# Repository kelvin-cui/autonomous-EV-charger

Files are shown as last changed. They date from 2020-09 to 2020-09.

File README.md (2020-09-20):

# autonomous-EV-charger

## Background
With the climate crisis that's happening right now, it's now more important than ever to take action and start adopting sustainable practices before we cause irreversable damage to our planet. A popular trend is the shift towards electric vehicles, and in an effort to make these vehicles more attractive, our team was tasked with creating an autonomous charger robot that would automatically find, and plug the charging line into the car after the car is parked. Our team is comprised of Anton Liu, Haoran Jayce Wang, and Kelvin Cui, and this project was created for our ESC204 (Praxis 3) class from the University of Toronto Engineering Science program.

autonomous

## Objective
Our objective was to create a robot that could locate the charging port of an electric vehicle, and plug in a standard charging plug. We wanted the robot to take up as little space as possible, be consistent and reliable, all while constraining ourselves to a budget of $300 CAD. 
Main

## How it works
The robot is controlled by a raspberry pi, using computer vision to determine the location of the port. Two IR distance sensors on each side of the bot determine the yaw of the bot with respect to the side of the car, and allow the bot to align itself perpendicularly. Stepper motors arranged in a square at the bottom of the bot allow the robot to rotate, and move in a straight line until it's directly in front of the charging port. Another stepper motor attached to a lead screw control a scissor lift mechanism that lifts the charging handle to the same height as the port. Finally, the robot moves forward to plug the handle in, where a limit switch lets the bot know when the handle is fully plugged in.
Plug-Quarter-View

## Design Process
In order to design this robot, we started by defining our stakeholders, our objectives, and our metrics to measure these objectives. Using this model, we started multiple rounds of design, going through many different alternatives until we finally arrived at our solution. If you're interested, you can see the detailed request for proposal here : 

**[Request for Proposal](https://github.com/ntnox/autonomous-EV-charger/blob/master/Request%20for%20Proposal.pdf)**

### Hardware Choice
Given our time and budget constraints, most of our electronics and sensors are simple, off the shelf components. We chose a raspberry pi as it allowed us to do complex computer vision analysis to find the charging port, with a raspberry pi camera. We chose IR distance sensors over ultrasonic sensors as they were more consistent, and delivered more accurate results in our range. For motors, we chose stepper motors, despite their increased complexity (more power draw and stepper motor drivers), as it would allow for finer control when compared to simple DC motors. Finally, we decided to go with a fixed power supply rather than a battery pack simply because it better fit our budgetary constraints. Finally, the omni-wheels were chosen to allow the rover to move freely, and rotate on the spot.

### Physical Design
Next came our design. We decided to model the entirety of our design, and take advantage of the rapid prototyping tools we had in our disposal. With a model, we were able to either lazer cut or 3D print all of our components.

Mechanical-CAD

While creating the model, we needed to make sure that from a strength perspective, our design would be feasible. As a result, we did FEA anaylsis of all of our structural parts to ensure that the parts wouldn't fail.

CAD FEA

### Electronic Design
For electrical design, we wanted to make sure that it was relaible, and we wanted it to be as easily repairable as possible should anything go wrong. As a result, our circuitry design is based on solderable breadboards for secure connections, with color coded wiring to easily distinguish the ciruits. In particular, since we had two power rails (5V and 24V), we used red wiring for all 5V, white for all 24V, and black for all ground. The main circuit was connected to the sensors, motors, and raspberry pi via JST headers, and could be easily taken out of the robot for repairs.

Electrical-Circuitry

### Software Design
- All the software is written in Python and executed by the onboard Raspberry Pi Zero. The goal of the software was to be able to autonomously detect the charging port and be able to align and navigate the charger into the charging port. The last developments made in the area of port detection used OpenCV to process frames from a live video feed to identify set markers on the charging port prototype. 
- Various methods were prototyped to experiment with the best approach to reliably identify and localize the robot with respect to the port through OpenCV that can be read about in the Programming folder, but the finalized approach was to use a red rectangle marked ontop of the port as the localization identifier. This method is the most reliable as our approach was to create a mask that only allowed pixels that match the redness of the marker and ultimately identify the contour of the rectangle in that mask. Since we knew exactly where our camera was placed on the robot, with some calibration and testing, we can then use the location of the rectuangular contour on the frame to localize the robot. To maximize the frames per second the robot is able to process using OpenCV, the task of generating the video stream from the camera and the processing of frames were completed on multiple threads or paralleled computations. This method was able to significantly improve our processed video stream from less than 10 fps to more than 15 fps.

- To control the movement of the robot, we utilized the integrated GPIO library in Python to output corresponding digital signals to control stepper motors as required
- Wireless communication for remote control of the robot from a laptop when required was built using the socket library in Python to create a server for sending desired commands to the rasberry pi and placing both the control laptop and the raspberry pi to be on one hotspot network so that they could communicate over the shared wifi. 

### Project Management
- Trello was used to manage this project, and this includes aspects such as due dates, person assigned, descriptions, categorization, etc. It gives us a clear view of the status of the project, and keeps us on track to complete it. We have also included a "Risks" section to identify potential failure modes of the design, and planned solutions for them. With trello, we were able to keep the project organized and efficient.

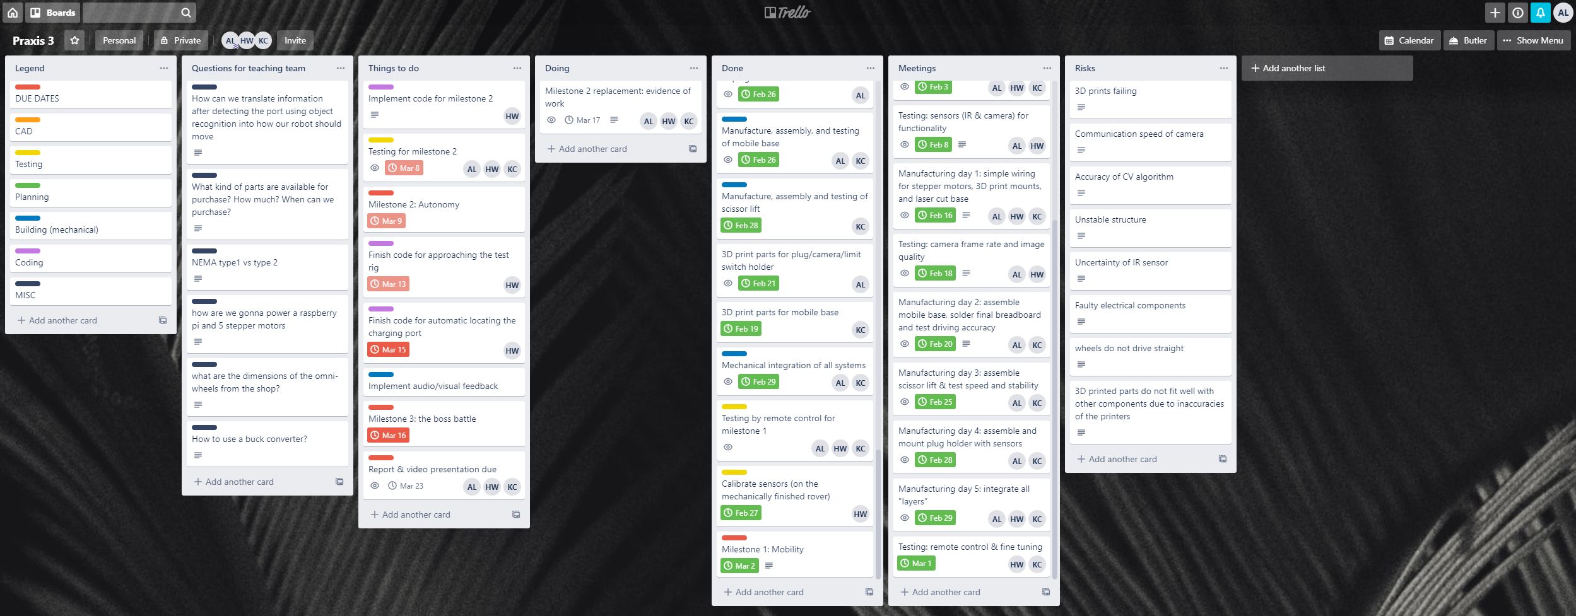
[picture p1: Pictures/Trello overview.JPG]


- We also used google sheets to create a Bill of Materials (BOM), which contains name, price, purchaser, and original URL of all the parts that we have used. As we are on a tight budget limit, the BOM helped us to identify priorities and where to cut costs. 

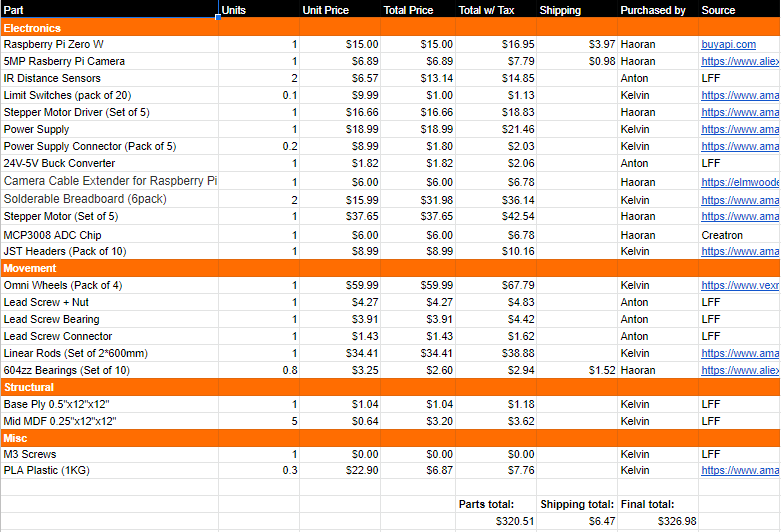
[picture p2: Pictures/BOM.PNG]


## Lessons Learned
If we were to do this project again, there are definately some things that we would do differently. The full raspberry pi was overkill, and a raspberry pi zero has enough computational power to do the calculations, at a fraction of the cost. The scissor lift design was a pain, since the motor did not linearly move the plug up and down. A vertical "elevator" design would have worked better, using the exact same hardware, with the lead screw directly driving the plug platform vertically.

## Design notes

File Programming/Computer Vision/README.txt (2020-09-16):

All code in the old testing folder were prototypes for old CV stratergies we tried to implement that we are no longer planning on using.
This includes:
	- Detecting the square profile of the cutout
	- Detecting the circular shape of the open port 
We scrapped these ideas because there is too much noise to filter out and too prone to error. In addition, alot of noise filtering would slow down the algorithm
alot as the Pi Zero is not as powerful as a laptop.

Instead our main stratergy was to apply a red filter (red_detect.py). This approach will be explained in more detail in the review and report but in short,
it is a method that will filter out all colours in the photo except for a certain shade of red, then we use that mask to do contour matching to draw rectangles.
We were planning on using a rectangular piece of red electrical tape on the top horizontal edge of the port. This algorithm is not only less 
computationally expensive versus other filters that use built in cv2 noise filtering functions, but also is alot more reliable and less conditions need
to be checked to ensure we are detecting exactly what we wanted to through rectangle ratios and areas.

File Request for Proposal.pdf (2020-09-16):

Anton liu 1005102407 | Wei Hai Cui 1005337324 | Haoran Wang 1004927163

## ESC204: Project Proposal

Problem Framing
In an effort to support the transition to renewable energy and make electric cars more viable and attractive, this project aims to make the use of electric cars more convenient for its owners by allowing the car to be autonomously charged when parked while respecting the current charging method in using a plug-in charger. This way, electric cars will be more reliable as the owner of the car will never have to worry about it not being charged for its next use or having to go out of their way to specifically charge their car.

The proposed design for this opportunity is a rover
style robot that can move independently in the x,y, and z-axis in addition to rotational abilities to match non-zero yaw of the port relative to the y-axis as defined in Figure 1 [1]. In addition, beyond the baseline functional objectives outlined in
the project guidelines, our team has decided to focus our
design on adapting to Additional settings A1, A2, and all of C

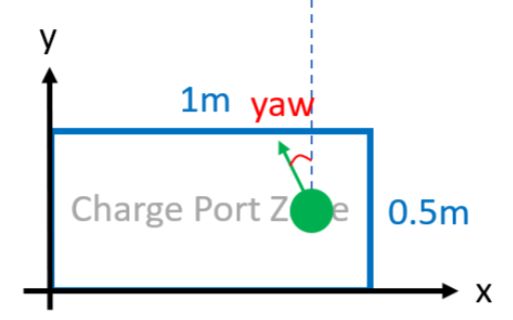
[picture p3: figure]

(4 degrees of freedom in port). | Figure 1: the charging port location [1]

Based on the values of stakeholders in this design opportunity such as us the design team, possible future users and manufacturers of this product, we have chosen to focus on the following objectives:

Global Design Objective | Sub-Objective | Justification | Design Impacts
| Minimize Failure Chances | -Want the robot to be functional and properly serve its purpose -Ensures the robot is fully functional during evaluation -Robot should be adaptable to various environments if implemented in the real world | Use of feedback loops in programming for real-time adjustment Verification of structure through FEA Use of stepper motors for different modes of operation
| Maximize Fault Tolerance | -In the event of an unexpected occurrence or failure, the robot should be able to continue its duty -Safety measure to ensure the | Redundancy in systems Use of feedback loops in programming for real-time adjustment

Reliability

| | robot does not completely fail if an unexpected failure occurs during the evaluation
Simplicity | Simplicity in design and fabrication | -Should be simple enough for us to realistically fabricate given our academic schedules | Use of simple linear mechanical and control systems
| Should be designed with simple parts | -Easy to fabricate -Easy to mass produce -Simple stress testing/simulation computations | Heavy use of 3D Printing and Laser Cutting
Usability | Functionality | -Must perform the task it was designed to perform -Should meet baseline and additional functional objectives to maximize grade gain | Simple control system (linear motion in each axis)
| Portability | -Allows the device to be easily transported by any stakeholder -Allows stakeholders to easily store the robot in their garage or other storage facilities | Simple part shapes for easy storage and transportation, Minimize area required for storage
Cost | Minimize Cost | -Must minimize cost to meet cost constraints. -Minimizes future production costs | Optimizing resource use (IE fitting as many cuts on one wood stock for laser cutting)
Safety | Hazard Prevention | -There should be no exposed moved parts that could harm any users -Users/owners of the device should not be in danger when within close proximity of the robot | All hazardous components (electrical and mechanical) are securely hidden and only accessible via purposeful use of tools
Modularity, Serviceability & Reparability | Minimize Repair time | -A minimal repair time allows for fast troubleshooting as required on evaluation day or during testing -Ensures the robot can remain | Layered design so each layer can be accessed for repair, troubleshooting for testing

| | functional for as long as possible
| Dimensional Adjustability | -Easily isolate required design changes to a single subsystem | Use of non-permanent fastening methods (bolts, rubber bands...etc)
Appearance & Style | Aesthetic appeal | -Aesthetically pleasing design allows for better marketability | Easily Identifiable logo Catchy Name Minimalist outer design

The following are the corresponding metrics that we have synthesized for each global design and sub-objective:

Global Design Objective | Sub-Objective | Metric | Proposed Test
Target | Constraint
| Minimize Failure Chances | Repeated testing should yield 100% repeatability regardless of test fixture conditions (floor type, test rig imperfections) [2] | Must be at least functional under specified testing/evaluation environment | Is the robot fully operational on smooth floors, tiled floors, and rough floors (Yes/No)
| Maximize Fault Tolerance | All Electronic Systems should have redundancy [3] | Non-redundant Electronic systems should be functional | How many of the three fundamental characteristics of fault tolerance does the system comply with? (Replication, Redundancy, Diversity)(See Sources for definition) [3]
Simplicity | Simplicity in design and fabrication | Should have a fully operational robot with all subsystems working as intended. | Must be within the scope of 2nd year engineering students | /
| Should be designed | All parts should be designed with regularly | N/A | How many irregularly shaped

Reliability

| with simple parts | shaped components [4] | | components does design have? [5]
Usability | Functionali ty | Achieve all objectives listed on project guideline | Must achieve at least the base goal | How many objectives can be met with the design?
| Portability | Should take up less floor space than 0.48m x 0.825m [6] | N/A | How much floor space does the assembled and disassembled robot take? (in m^2)
Cost | Minimize Cost | Cost should be less than $250 | Must be less than $330 | Sum the cost of all parts in BOM
Safety | Hazard Prevention | Should be designed with minimum number of accessible moving parts with no moving parts exposed [7] | Must have an emergency shutoff switch | How many moving parts are exposed? Can moving/internal parts be accessed without tools? [7]
Modularity, Serviceability & Reparability | Dimension al Adjustabili ty | Should be constructed with fully non-permanent fastening methods for easy access and repairability[8] | Must have no loose components during operation | Number of non-permanent fastening methods vs permanent ones

Alternate Designs
Apart from our final rover design, we also considered a robotic arm-based design, as well as a stationary gantry design. These designs were chosen as our top three alternatives through multiple converging and diverging stages, using tools such as Morph Charts in order to come up with ideas and then trim them down.

The Robotic Arm was considered due to it’s mechanical simplicity and modularity. It would only require 4 motors in order to move all the axis, and it would be relatively cheaper to manufacture, due to the minimal requirements for parts such as pulleys, belts, and lead screws. Furthermore, as it would have a stationary base, the robotic arm would easily fulfill some requirements, such as returning to home. However, control systems from a complex robotic arm would not be within the scope of the skillset of the design team as none of us have experience with control theory.

Figure 2: Reference Arm Design

The Stationary Gantry design was selected for its programming simplicity - as each axis of movement in the cartesian system would be controlled by one motor. Similarly to the Robotic Arm, it would also be stationary, which again allows us to better track exactly where the charging arm is, relative to a home position.

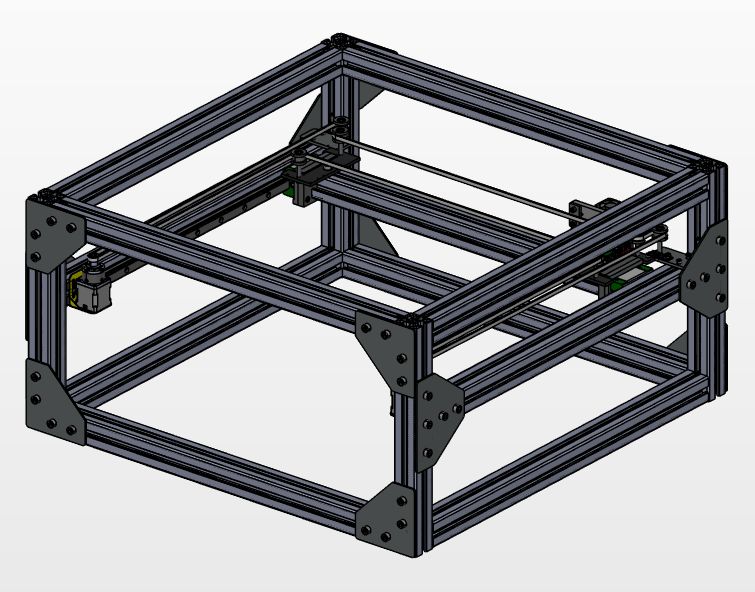
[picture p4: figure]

Figure 3: CAD model of the reference Gantry Design Convergence Process
After our convergence process, we selected the Rover Design, as it best fit our criteria. However, it took us many rounds of converging and diverging in order to reach this decision.
For our first round of diverging, we simply brainstormed ideas in order to start a list of possible options (See Appendix A). However, we kept in mind what we learned last year in Praxis 2 from Professor Sheridan, and decided to do our brainstorming individually, ensuring that our ideas wouldn’t be influenced by each other. Furthermore, in order to prevent anchoring, our team made an effort to prevent looking at reference designs, so that our ideas were as unique as possible.
From this round of diverging, we came up with many designs, which we needed to quickly cut down. After further familiarizing ourselves with the criteria, we used quick system 1 decisions to get rid of any designs that were simply unfeasible. For example, one of the ideas that we had was the tentacle arm that was shown in lecture - it was too complex as it pertained to continuum robotics [9] , and thus out of the scope of our design teams’ skillset.

Our team noticed that there was a lot of overlap in some of our ideas, and decided to categorize our designs two categories - Movement and Autonomy. In movement, we broke it down further into subcategories featuring movement in the different axes, as well as rotation for yaw. For Autonomy, the subcategories included the different features needed, such as hole locating, distance to hole, yaw detection, among others. These subcategories allowed our team to create a morph chart (See Appendix B) from all the ideas from the first round, allowing us to mix and match different designs as we saw fit.
At this point, we had created our objectives and DxFs, which we used to inform our decisions while we converged using tournament-style for each subcategory. From there, we combined the top three from each subcategory to create our top three alternate designs - the rover, the gantry, and the robotic arm.
For our final round of convergence, we originally decided to prototype each design, and see which ones would be the best suited to our needs. For the robot arm, we ran simple calculations to determine the amount of holding torque needed in the worst case scenario, which resulted in a torque of 2500N-cm (See Appendix D). When looking for stepper motors with that specification of holding torque, we found that ordinary Nema17 Motors would not cut it, and the Nema42 Motors required would not fit our budget.
The gantry design was also eliminated because of the material cost and low portability. For the gantry system to work, 30 feet of 1” aluminum extrusion is needed (not including connectors). According to McMaster-Carr, 10 feet of the material cost $30.54 USD [10], which means the structure alone will consume at least half of the budget (approximately $120 CAD in total). With other components needed, we would likely exceed our budget constraint. Also, the structure is estimated to be 1.5m*0.5m*1m in size in order to reach all possible port locations, which does not comply with our usability/portability objective when compared to the other two designs,
Finally, we needed to prove that the Rover design was possible. Our two key concerns were the structural strength of the scissor lift, as well as straight-line movement with omni wheels.
We first ran key structural components, such as the base, and the scissor arms through Ansys FEA to validate its strength, letting us test our design without having to make physical prototypes. For the base, our team also checked deflection, since we were advised that omniwheels are sensitive to weight distribution. Calculating a weight of ~20N on the base, we used a factor of safety of 2.0 and tested for a case of 40N. With ½” Plywood as the main base, the deflection was negligible, while the stress was well below the yield strength of the plywood.

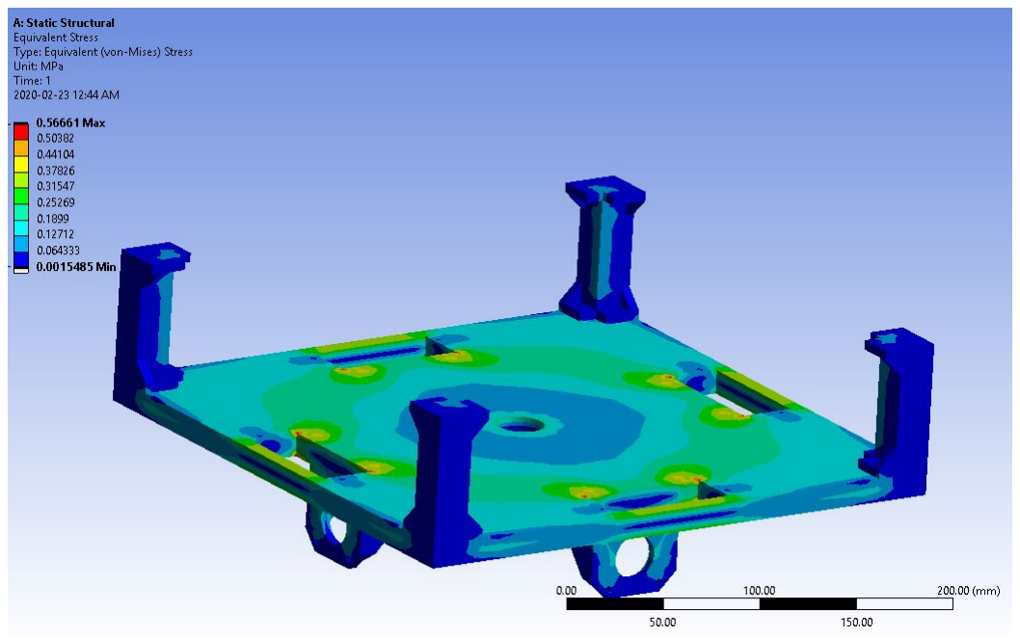
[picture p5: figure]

Left - Figure 4: Deflection simulation with 40N. Max deflection (shown in red) is 0.08mm. Right - Figure 5 : Equivalent Stress with same load. Max Stress (red) is 0.5MPa.

Then, created a 1:1 prototype of the base, and tested it’s mobility. Luckily for us, the robot was able to consistently move in straight lines, without any issue of straying.

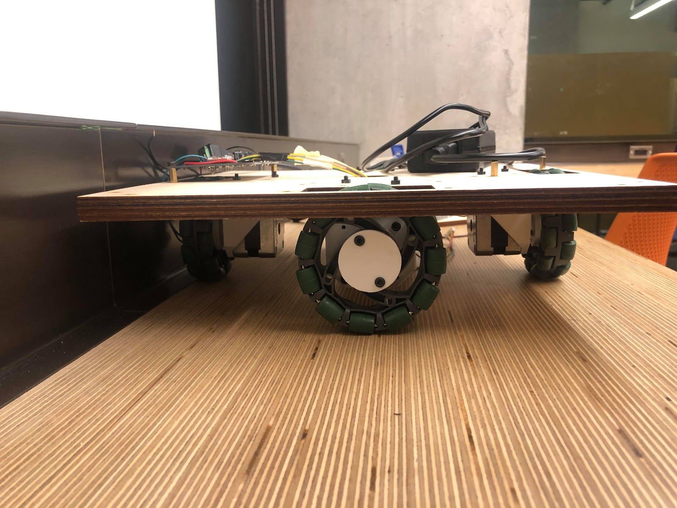
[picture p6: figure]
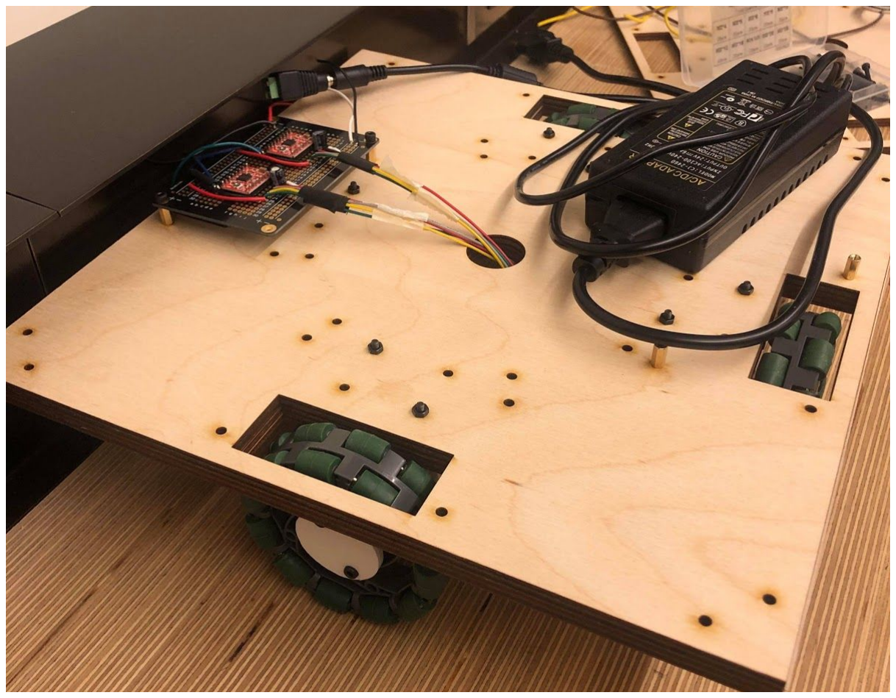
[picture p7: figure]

Figure 6 and 7 : Prototype Rover Movement

Similarly, the scissor arms were another component that we would be able to verify without physical prototyping. Its max load case would be when it was fully extended, as there would be an additional moment on the arm, due to its layout. With a weight of ~1.35kg on top of the scissor lift, we used a load case of 27N, which encompassed a FOS of 2.0. This load resulted in a max stress of 2.4MPa, which once again was well within the limits of the Plywood.

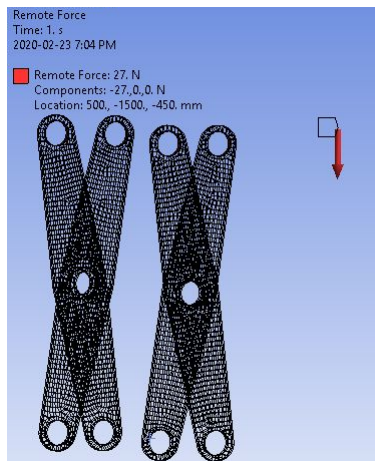
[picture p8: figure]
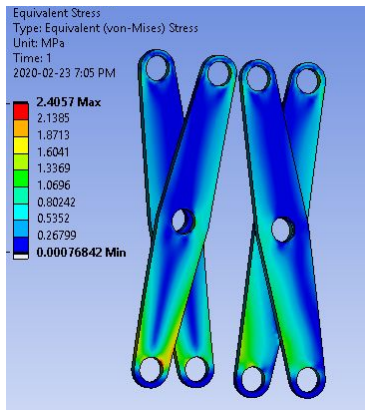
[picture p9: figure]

Left : Figure 8 : Load Definition, with the Red Arrow representing remote force of 27N. Right: Figure 9: Equivalent Stress with same load.

During this time, we also prototyped the CV portion, with a calculation rate of ~30 frames a second, which was more than what we needed to get accurate data (see figure 16).

### Proposed Design Solution

Mechanical and Electrical Design

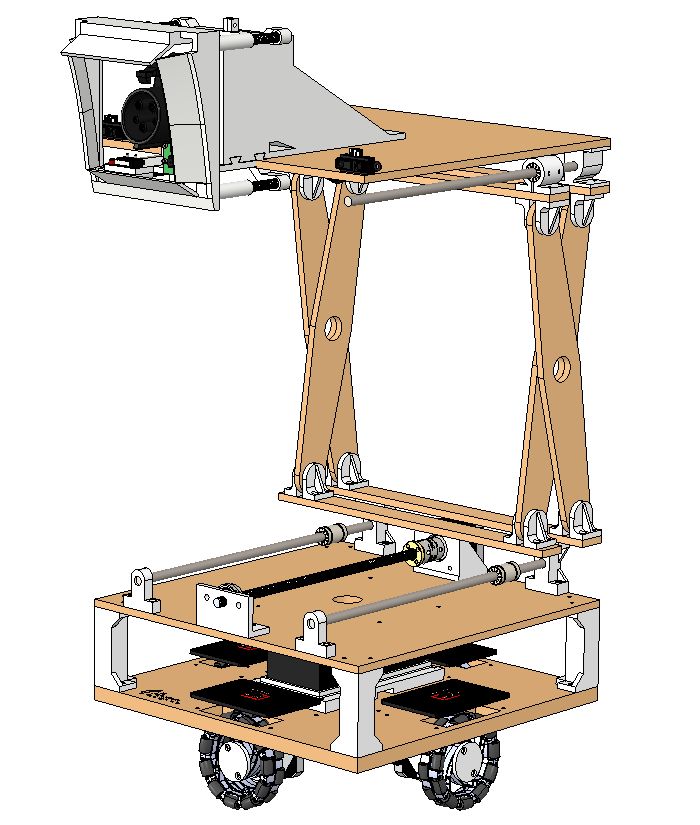
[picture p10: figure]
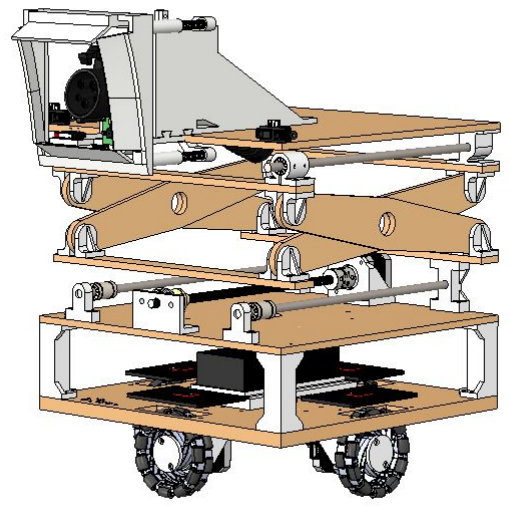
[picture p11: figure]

Figure 10 and 11 : Proposed Rover Design (left), with full z-extension (right). Parts shown in white are 3D printed, while parts shown in brown are laser cut.

The proposed design solution is a rover style robot with 4 omni-wheels arranged in a square formation, driven by stepper motors with two wheels driving in the x and y-axes respectively, as shown in figure 8. Movement in the z-axis is controlled by a single joint scissor lift, which is controlled by a stepper motor and lead screws, with steel rods and bearings allowing for minimal friction, seen in figure 9. This mobility system allows the robot to move in any axis independently to allow for simple control programming. In addition, the arrangement of the omni-wheels in a square formation allows for in-place rotation to address a varying yaw angle in the port.

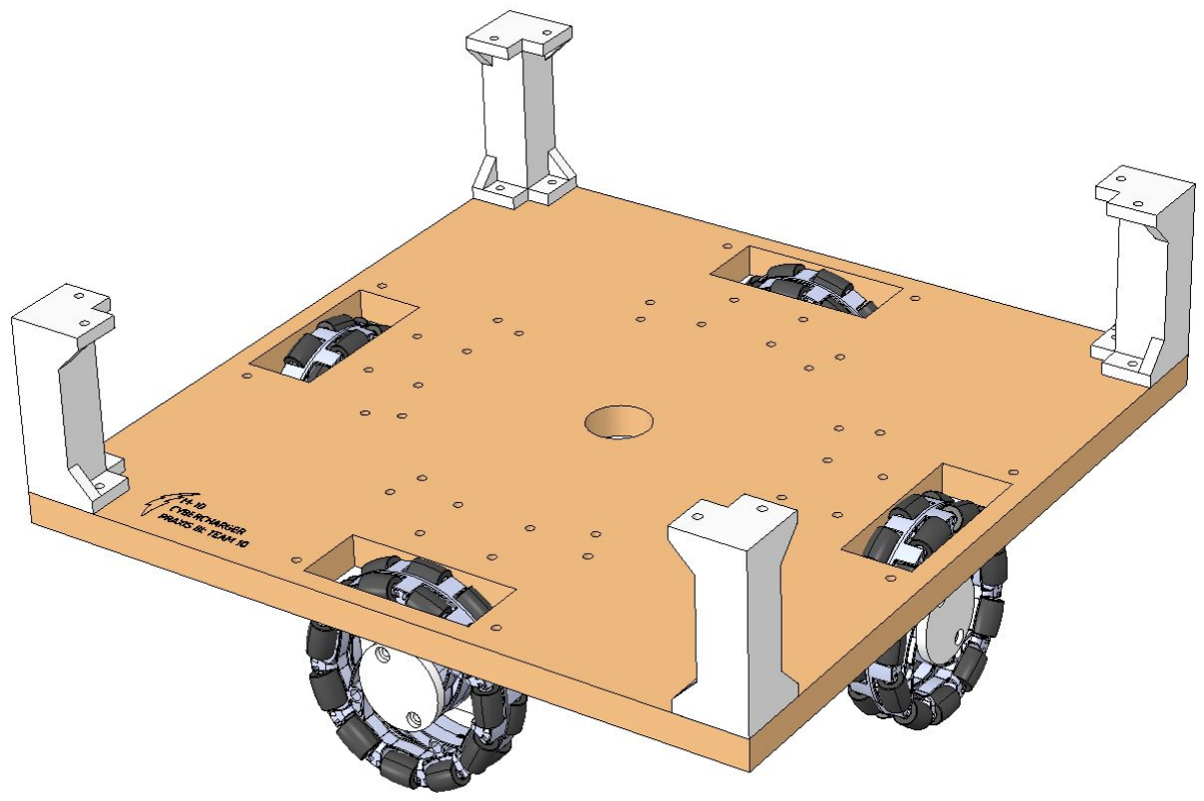
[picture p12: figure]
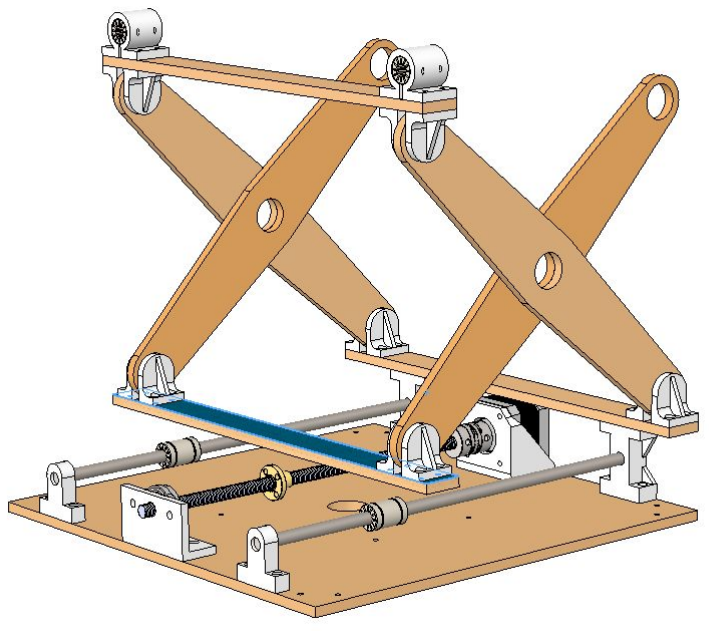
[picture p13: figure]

Left - Figure 12 : Base Design, with 4 Omni Wheels, as well as mounting holes for electronics. Right - Figure 13: Single Joint Scissor Lift

The scissor lift sits on top of a multilayered mainframe that begins at the wheel level holding the stepper motors. Then, the main electrical components such as the raspberry pi, power supply, and solder-in breadboards are secured onto the base of the mainframe. This design allows for layers to be easily removed for modularity and repairability.
Equal weight distribution is achieved by offsetting the weight of the plug and mold with the weight of the stepper motor on the scissor section, and all other parts are symmetric, allowing for the most optimal distribution for the omni wheels. Furthermore, the heaviest components such as the ½” base, power supply, and four stepper motors are as low as possible, lowering the center of gravity, further minimizing our chances of tipping.
The plug is held by a 3d printed mold of it, which is screwed securely onto the top platform of the lift. The camera is mounted close to the plug for accuracy. A limit switch mounted beside the camera activates when the plug is inserted, giving raspberry Pi the signal that the task has been completed. There is a shroud in front of the plug. Its pyramidal shape corrects the plug if the sensors are not accurate enough, and it guides the plug to the correct location. After the plug is in the correct location, it retracts as the rover drives forward, letting the plug be inserted. To meet our modularity and ease of assembly/disassembly metric, the components are inspired by woodworking joints such as mortise and tenon joints and dovetail joints. Using these designs allow us to use the minimum amount of screws, which decreases assembly/disassembly times, decreases hardware costs, and modularises the components.

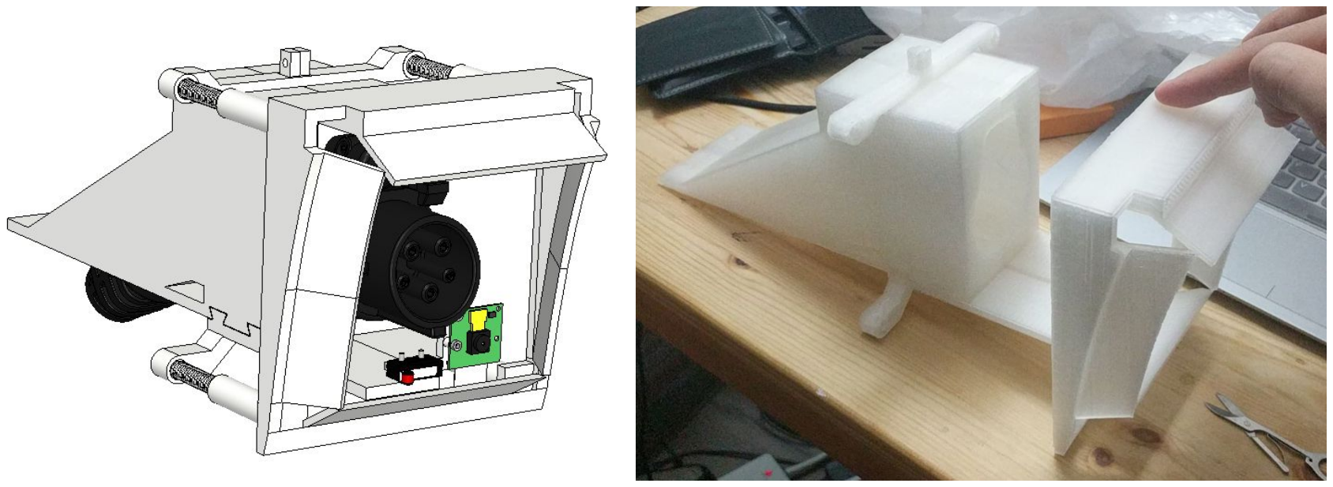
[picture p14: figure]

Figure 14: CAD Design of plug holder | Figure 15: prototype 3D printed parts of the holder

Autonomous Systems Design
A Raspberry Pi Zero W is the main onboard controller of our robot while computer vision + IR sensors are used in the autonomous location of the charging port. The Pi controls all of the motors on the robot via its GPIO ports while providing image data via the raspberry pi camera module. The IR sensors will be used to find the yaw of the port while the computer vision will calculate how much the robot has to move in the x and z-axis knowing the marker/port length in both distance units and pixels. This allows us to obtain a conversion factor between centimeters and pixels and thus converting that value into how much our motors need to turn. Our options are detecting the whole port or a black non-reflective square taped on top of the port in the middle so that we can use the OpenCV threshold function and make everyone pixel white except for those in the black circle

(cv2.THRESH_BINARY_INV). A limit switch below the charger will rely if the charger has been successfully plugged in or if readjustment is needed.

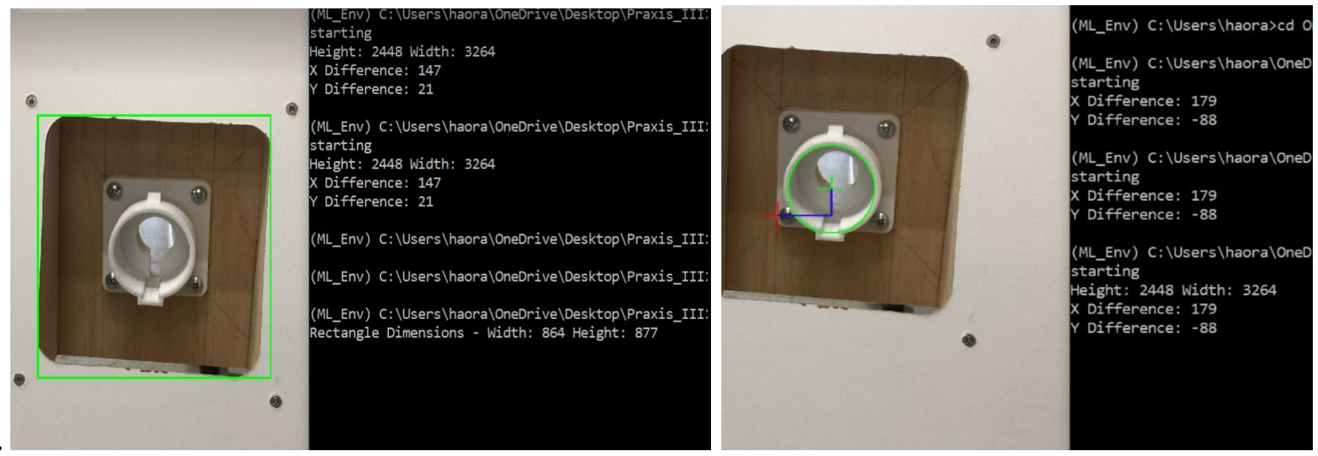
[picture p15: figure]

Figure 16: Preliminary detection of port and port hole using OpenCV. Red crosshair is center of image

System Strategy

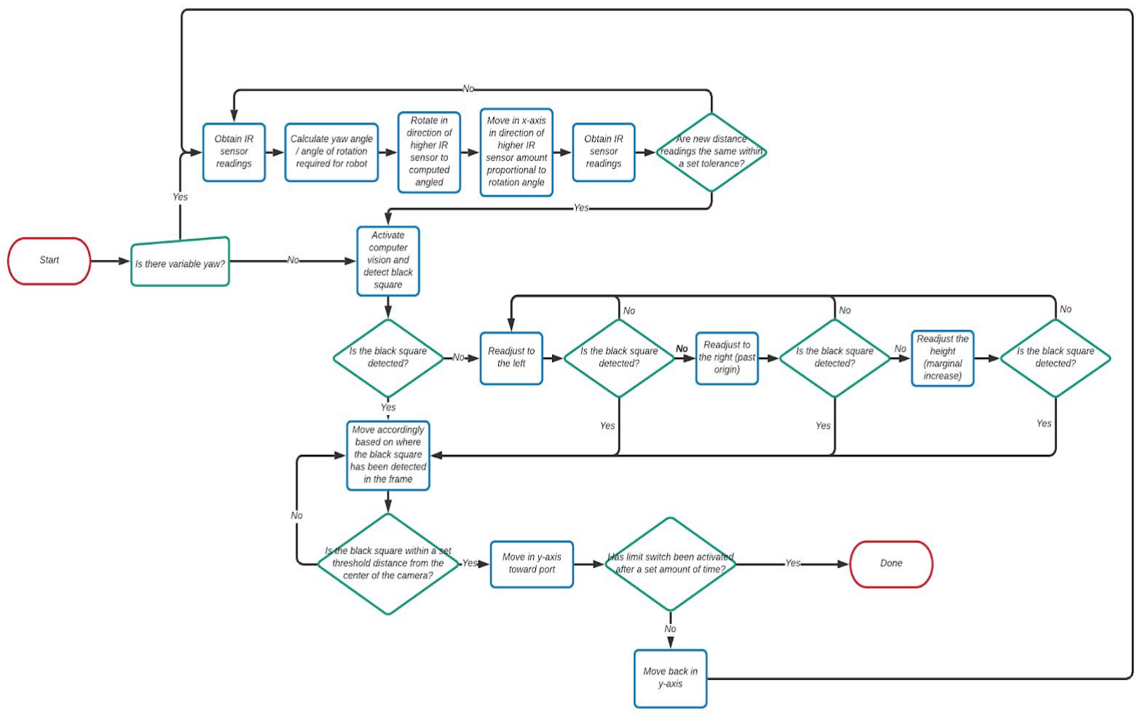
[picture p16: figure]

Figure 17:Flowchart for System Strategy

Risk Assessment
After conversing with some TAs during work sessions, we learned that uneven weight distribution in the body of our robot might affect whether or not the Omni wheels will traverse in a straight line, so thorough testing and symmetrical distribution of components is required to ensure that the wheels travel in as straight a line as possible whenever required.

Next, uncertainties in IR sensor measurements will also contribute to inaccuracies in the rotation of the robot in relation to the actual yaw angle. We try to account for this by using braces around the charger that ideally would guide the charger into the port regardless of inexact yaw angles.

Although preliminary testing of the computer vision software is done on a video feed, it is still uncertain how the algorithm will perform when the robot is in motion and accidentally captures extremely blurry images. Furthermore, while optimization of the computer vision algorithm can be done, as the background behind the test rig is completely random, it is uncertain if the computer vision algorithm will mistake anything in the background as a result of image noise or coincidental patterns from unexpected lighting conditions. Tests in various backgrounds and lighting conditions will have to be done to minimize the risk of failure due to an algorithmic misclassification. In addition, the speed of the robot will be adjusted to ensure usable photos are taken at every step.

Bill of Materials (Preliminary)

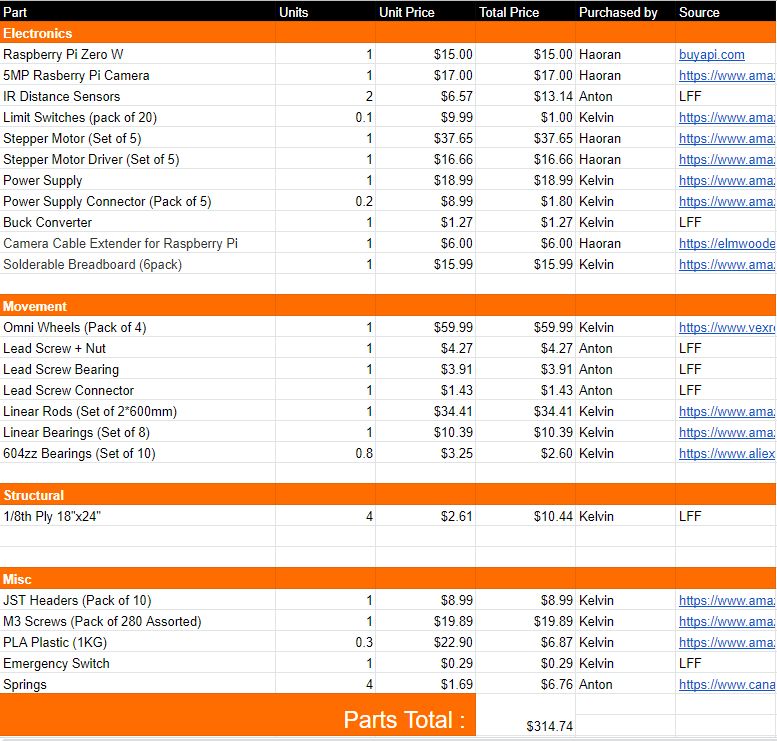
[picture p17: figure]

Figure 18 : Bill of Materials for the team, last updated on February 23, 2020

Project Management
We used Trello to manage the progress and responsibility of this project. In the Trello board, there are many lists: Legend, Things to do, Doing, Done, Meetings, Questions for teaching team, and

Risks. These lists help with identifying the status of tasks and makes the board very easy to navigate through. Inside the lists, cards are created with the name of the tasks, along with members responsible, due dates, proper categorization, and explanation.

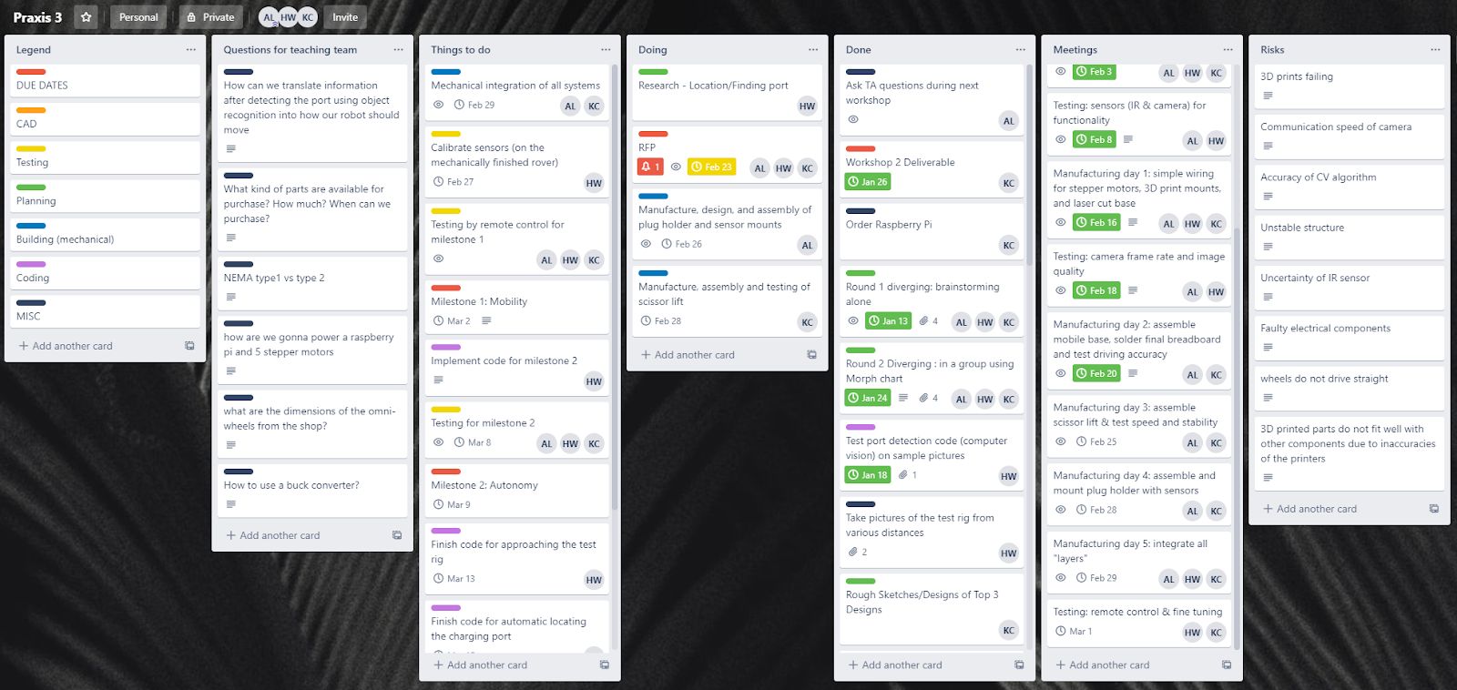
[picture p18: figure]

Figure 19: Overview of Trello board

The legend provides explanations of color coding, which makes navigating the board easier. For example, if someone wants to find something related to mechanical construction, they just need to look for blue markers.

Questions for the teaching team is a place to put our questions; it can be either about clarification of the project or technical details. Answers to those questions will be recorded in the description section of the card.

Things to do, doing, and done are lists that label the completion status of the tasks. The tasks within are crucial to the project because the timeline needs to be followed strictly in order to meet the milestones. Detailed explanations are provided for each task, and pictures are provided as evidence for completion.

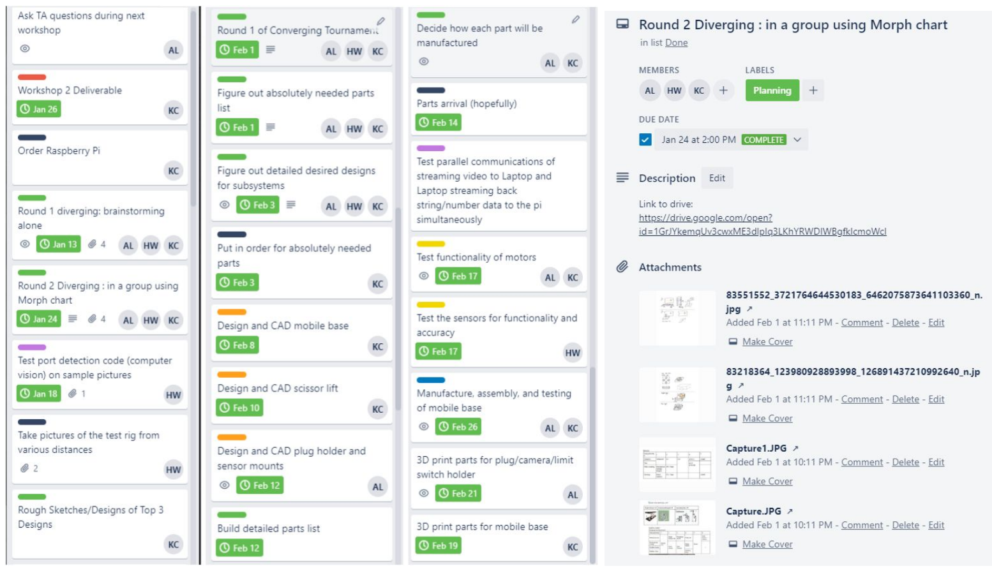
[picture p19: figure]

Figure 20: Examples of tasks in the done category Figure 21: One of the tasks

The meetings section show completed and planned meetings between members and the main cause for the meeting, along with the attendees. These meetings can be in person or online through video calls. After the meeting, the notes/minutes are recorded in the descriptions of the cards for easy access.

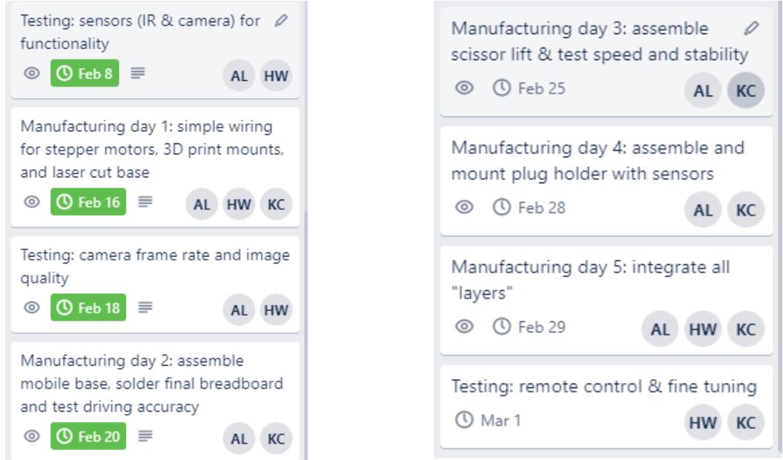
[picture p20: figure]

Figure 22 : Examples of past meetings Figure 23: Examples of planned future meeting
The risks section highlights potential risks and how to solve them on the event of the problem occuring. This section helps us to prepare for failures in our previous design processes. However, many unexpected problems can occur and this section is being updated constantly.

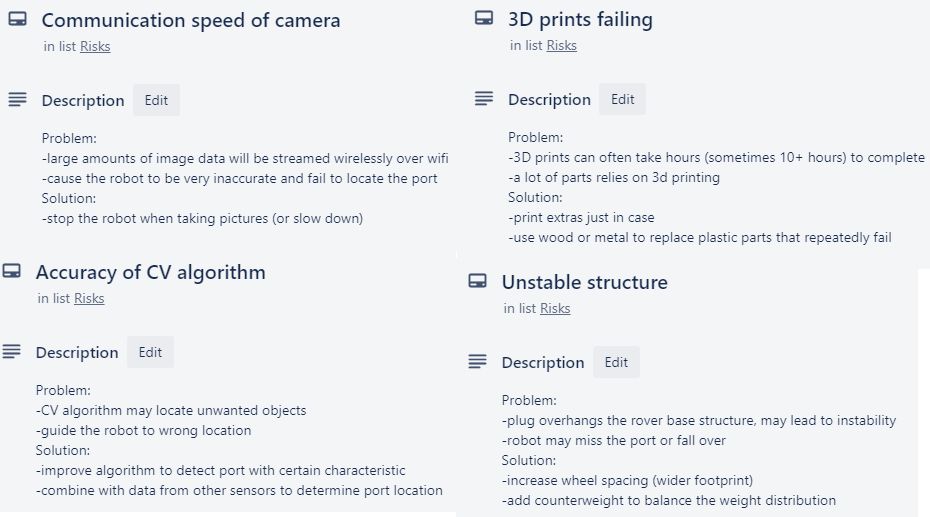
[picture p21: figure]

Figure 24 : Examples of risks and appropriate solutions

Using the Trello board, the team can work efficiently with easy communication and clear goals. The board allows all team members to be aware of their own tasks and lets the team be on track to complete milestones. So far, all tasks have been completed successfully and on time with little to no issues.

Project Timeline
Week 1 - Jan 6 to Jan 13:
- Receive project
Week 2 - Jan 13 to Jan 20:
- Round 1 diverging: brainstorming alone (Individual)
- Test port detection code (Computer Vision) on sample pictures (Haoran) Week 3 - Jan 20 to Jan 27:
- Round 2 diverging: in a group setting with morph charts (Everyone) Week 4 - Jan 27 to Feb 3:
- Round 1 converging: tournament & Pugh chart. (Everyone)
- List absolutely needed parts and purchase them (Everyone)
- Decide on three alternate designs (Everyone)
Week 5 - Feb 3 - Feb 10:
- More detailed designs of the three alternate designs (Everyone)
- Decide on a single design (rover)
- Design and CAD mobile base (Anton, Wei Hai)
Week 6 - Feb 10 to Feb 17:
- Design and CAD scissor lift (Wei Hai)
- Design and CAD plug holder and sensor mounts (Anton) Update: camera mount relocated to front of plug instead of above
- Build detailed parts list (Everyone)
Week 7 - Feb 17 to Feb 24:

- Decide how each component will be manufactured (Laser cutting, 3D printing) (Wei Hai, Anton) Update: laser cutter does not cut ½” inch wood so stack 4*⅛” instead, adjust tolerance in CAD because of 3D printer accuracy
- Test communication between Laptop and raspberry Pi (Haoran) Update: Wireless communication is no longer used, all computations are now done locally on the pi
- Test stepper motors (Anton, Haoran)
- Test sensors for functionality and accuracy (Haoran)
- Test camera frame rate and image quality (Haoran)
- 3D print parts for mounts (Anton, Wei Hai)
- Assemble and Prototype mobile base (Everyone) Week 8 - Feb 24 to Mar 2:
- Manufacture scissor lift (Anton, Wei Hai)
- Manufacture plug holder and sensor mount (Anton)
- Integrate mechanical system (Everyone)
- Testing with remote control (Haoran)
Week 9 - Mar 2 to Mar 9: Milestone 1 Progress Evaluation
- Implement and test code for milestone 2 (Haoran)
- Repair any mechanical issues that occur during testing (Anton, Wei Hai) Week 10 - Mar 9 to Mar 16: Milestone 2 Progress Evaluation
- Implement code for milestone 3 (Haoran)
- Implement audio/visual feedback when plug is inserted (Anton, Wei Hai) Week 11 - Mar 16 to Mar 23:
- Test and improve functionality of robot (Everyone)
Week 12 - Mar 23 to Mar 30: Milestone 3 Final Evaluation
- Ensure robot can complete the milestone (Everyone)
- Work on final report & video presentation (Everyone)

Source Extracts
[1] - ESC204: Project Guideline V1.0 Section 2.3.2 - Figure 11
[2] - Daley, Daniel T.. (2011). Design for Reliability - Developing Assets That Meet the Needs of Owners - 4.2 Defining DFR. Industrial Press. Retrieved from https://app.knovel.com/hotlink/pdf/id:kt0098VX34/design-reliability-developing/defining-dfr
[3] - Kaboli, Shahriyar Oraee, Hashem. (2016). Reliability in Power Electronics and Electrical Machines - Industrial Applications and Performance Models - 11.2 Redundancy. IGI Global. Retrieved from
https://app.knovel.com/hotlink/pdf/id:kt010YSCO2/reliability-in-power/redundancy
[4] - Kutz, Myer. (2019). Handbook of Farm, Dairy and Food Machinery Engineering (3rd Edition)
- 16.8.1.2 Container Geometry. Elsevier. Retrieved from https://app.knovel.com/hotlink/pdf/id:kt012286HE/handbook-farm-dairy-food/container-geometry

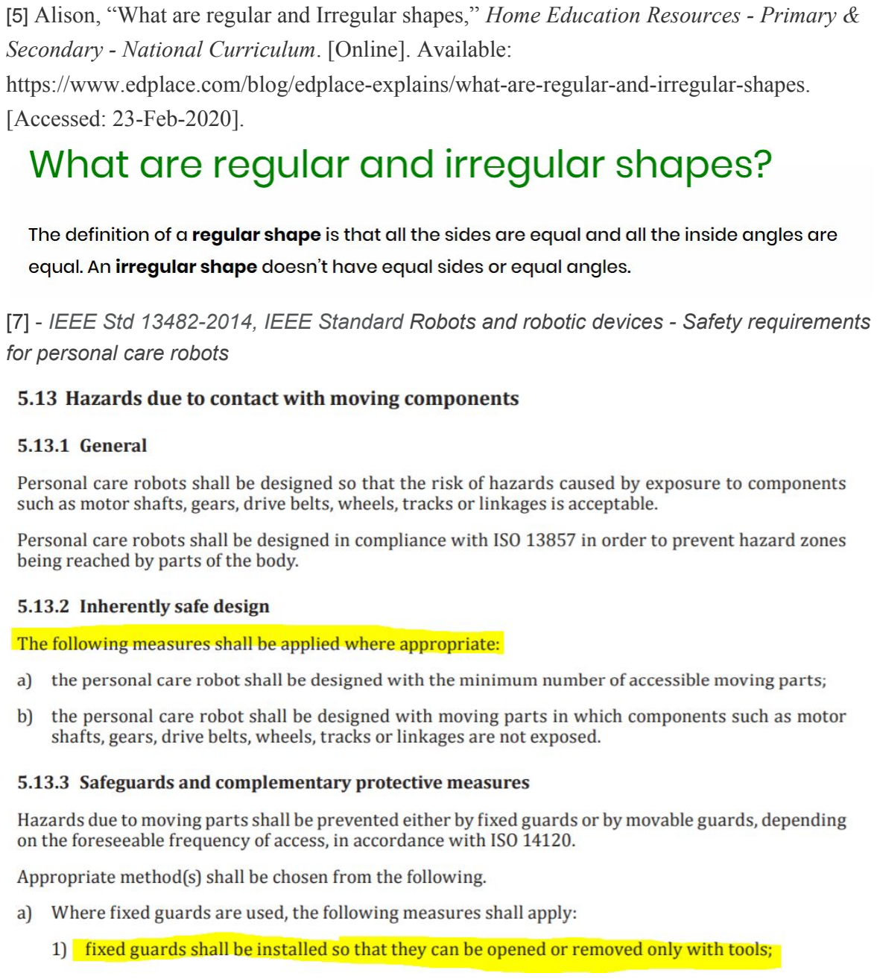
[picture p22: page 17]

[5] Alison, “What are regular and Irregular shapes,” Home Education Resources - Primary & Secondary - National Curriculum. [Online]. Available: https://www.edplace.com/blog/edplace-explains/what-are-regular-and-irregular-shapes. [Accessed: 23-Feb-2020].
[7] - IEEE Std 13482-2014, IEEE Standard Robots and robotic devices - Safety requirements for personal care robots

[8] - Kosky, Philip Balmer, Robert Keat, William Wise, George. (2010). Exploring Engineering -An Introduction to Engineering and Design (2nd Edition) - 20.5 Design for Adjustability. Elsevier. Retrieved from
https://app.knovel.com/hotlink/pdf/id:kt00TY3631/exploring-engineering/design-adjustability

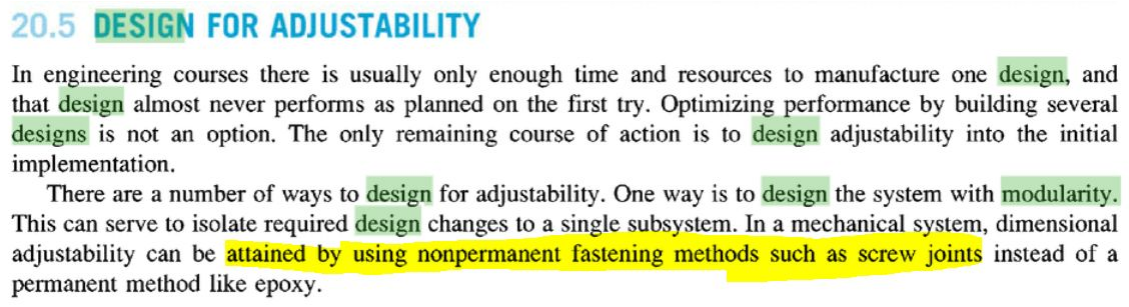
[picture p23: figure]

[9] - Walker I.D., Green K.E. (2009) Continuum Robots. In: Meyers R. (eds) Encyclopedia of Complexity and Systems Science. Springer, New York, NY
[10] - McMaster-Carr. [Online]. Available: https://www.mcmaster.com/aluminum-extrusions. [Accessed: 24-Feb-2020].

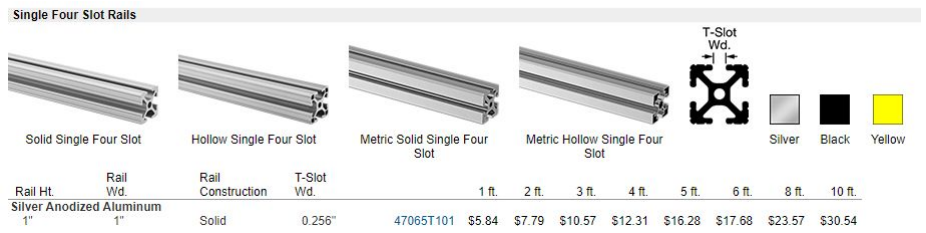
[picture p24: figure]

Appendix A: Brainstorming Evidence

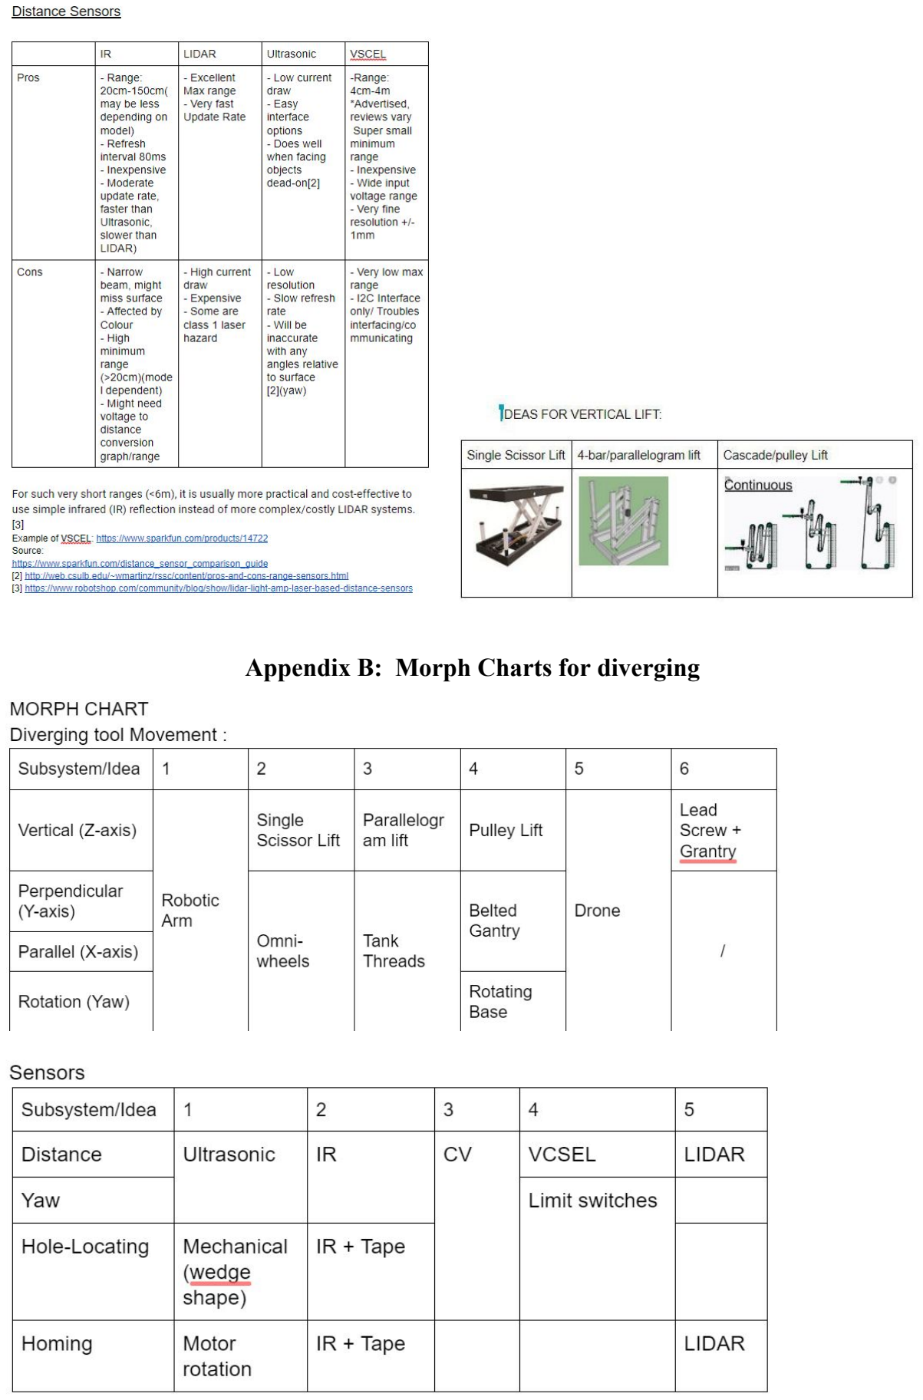
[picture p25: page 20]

Appendix B: Morph Charts for diverging

Appendix C: Pugh Charts for converging

Appendix D : Calculations

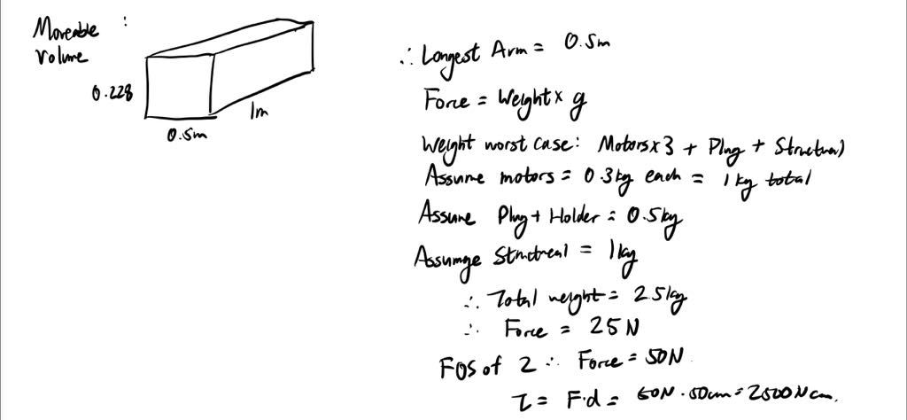
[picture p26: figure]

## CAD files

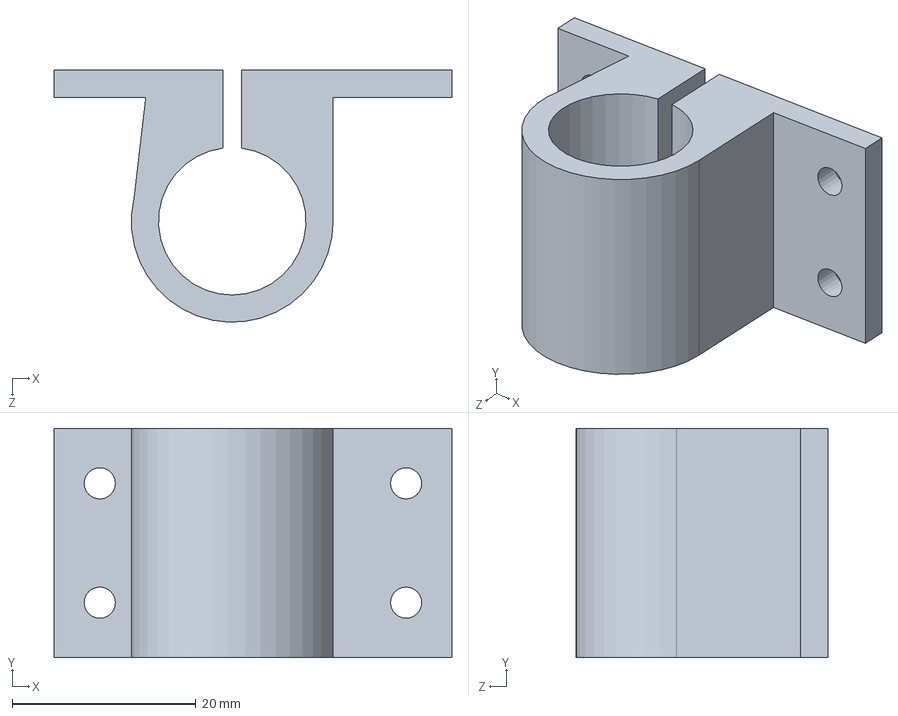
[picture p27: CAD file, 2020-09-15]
CAD/Top LM8UU Mount.sldprt
43.4 x 25.0 x 27.5 mm

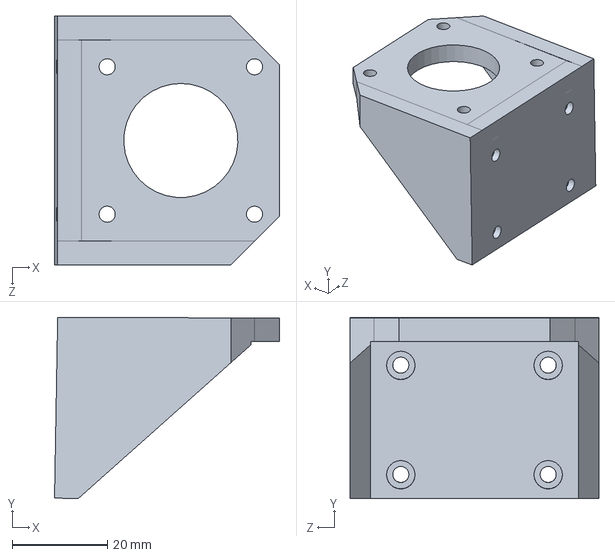
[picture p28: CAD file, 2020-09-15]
CAD/Stepper_Mounts.sldprt
47.3 x 38.1 x 52.3 mm

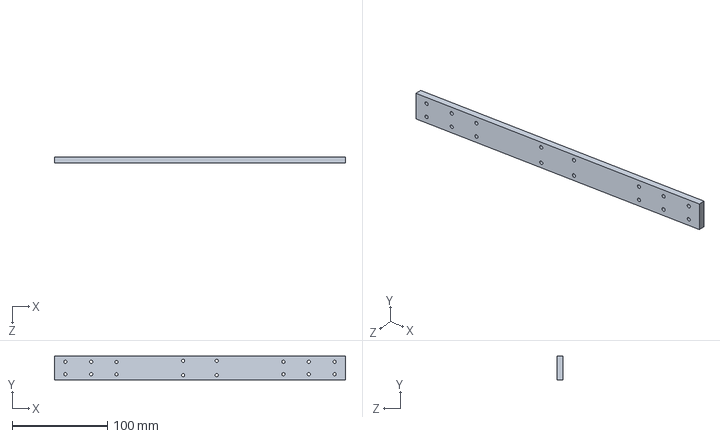
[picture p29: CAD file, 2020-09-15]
CAD/Ply-Scissor-Bottom Front.sldprt
304.8 x 25.0 x 6.35 mm

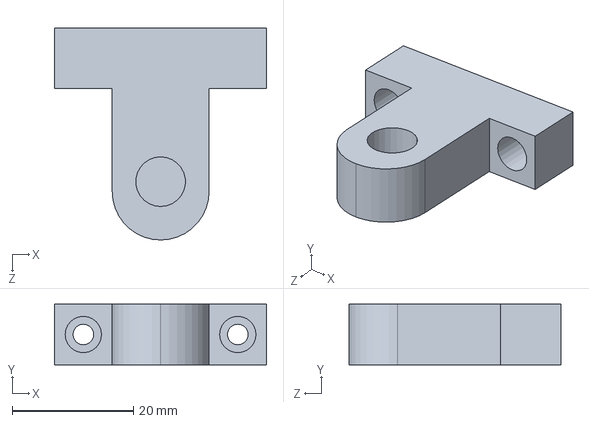
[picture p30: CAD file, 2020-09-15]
CAD/Rod_Mount.sldprt
35.0 x 10.0 x 35.0 mm

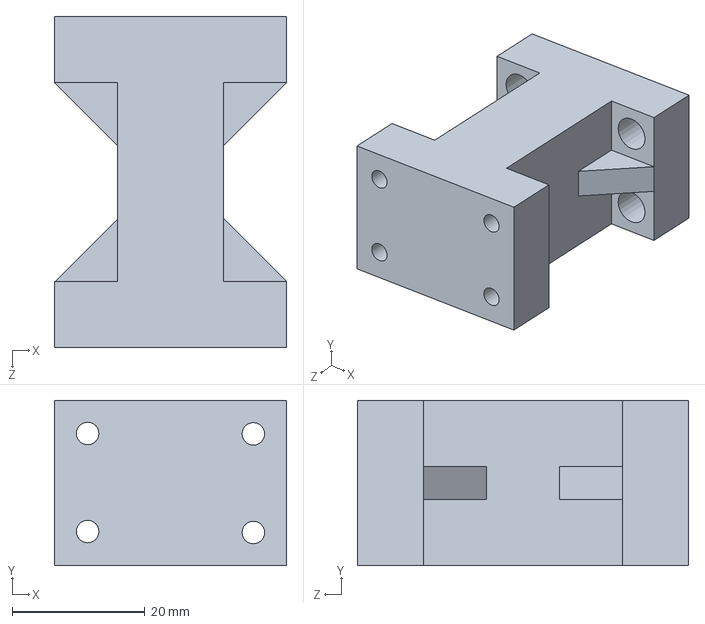
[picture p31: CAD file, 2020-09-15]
CAD/Front Rod Mount.sldprt
35.0 x 24.9 x 50.0 mm

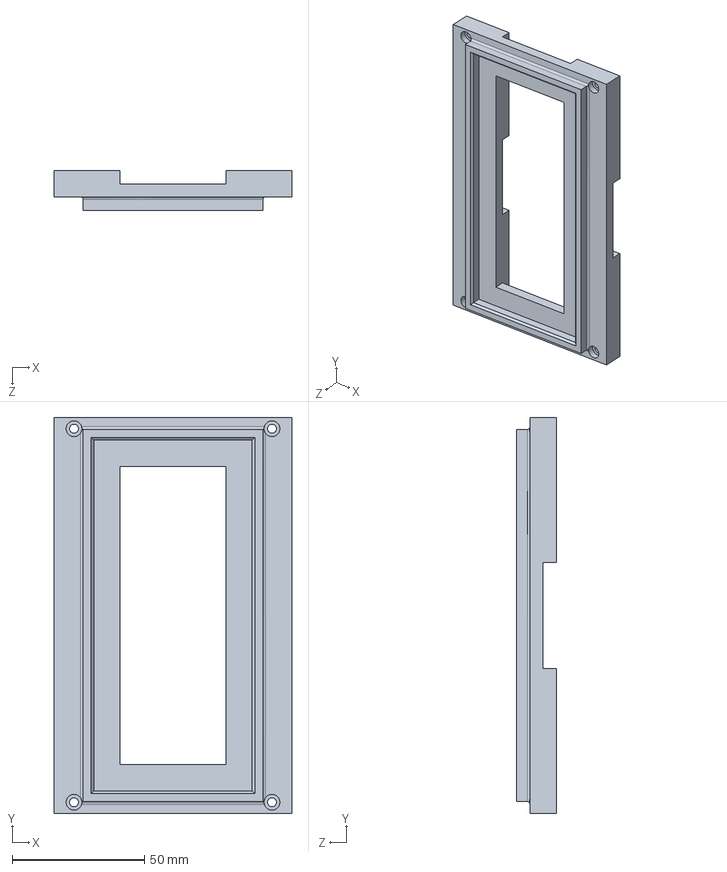
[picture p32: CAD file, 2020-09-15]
CAD/PSU_Mount.sldprt
90.0 x 150.0 x 15.0 mm

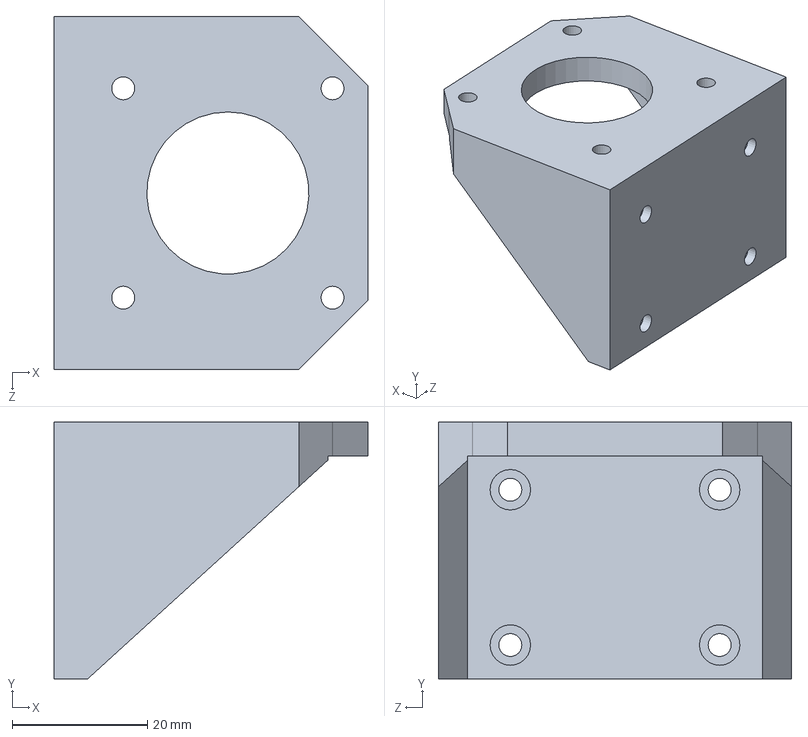
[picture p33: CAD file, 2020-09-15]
CAD/Stepper_Mounts_Top.SLDPRT
46.5 x 38.0 x 52.3 mm

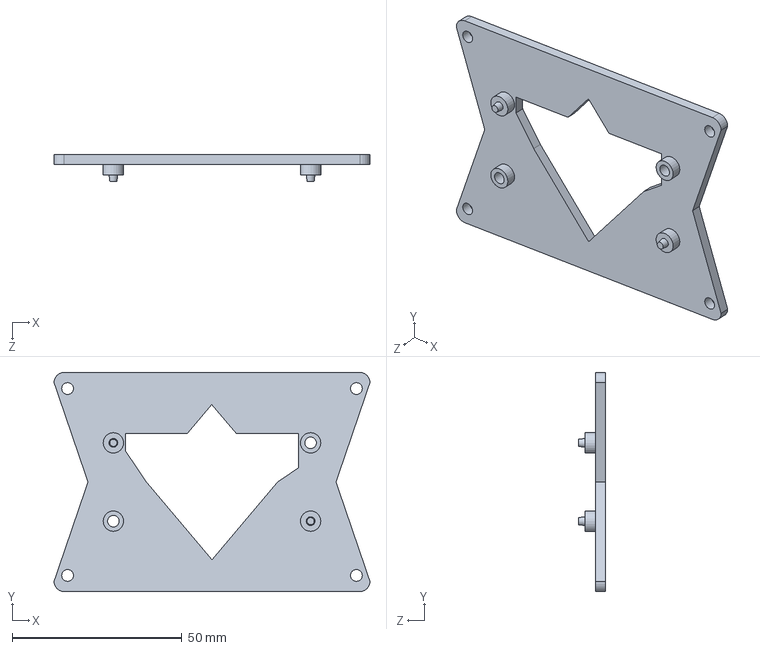
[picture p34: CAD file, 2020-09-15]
CAD/Pi Holder.SLDPRT
93.0 x 64.5 x 8.00 mm

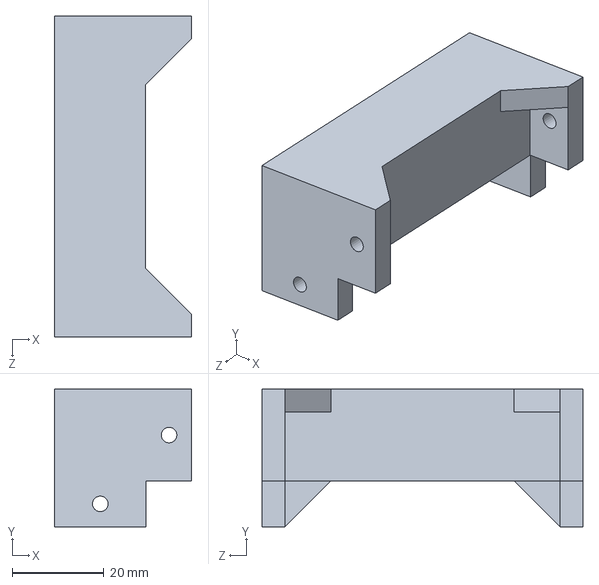
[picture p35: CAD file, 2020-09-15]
CAD/Upright-Supports.SLDPRT
29.9 x 30.0 x 70.0 mm

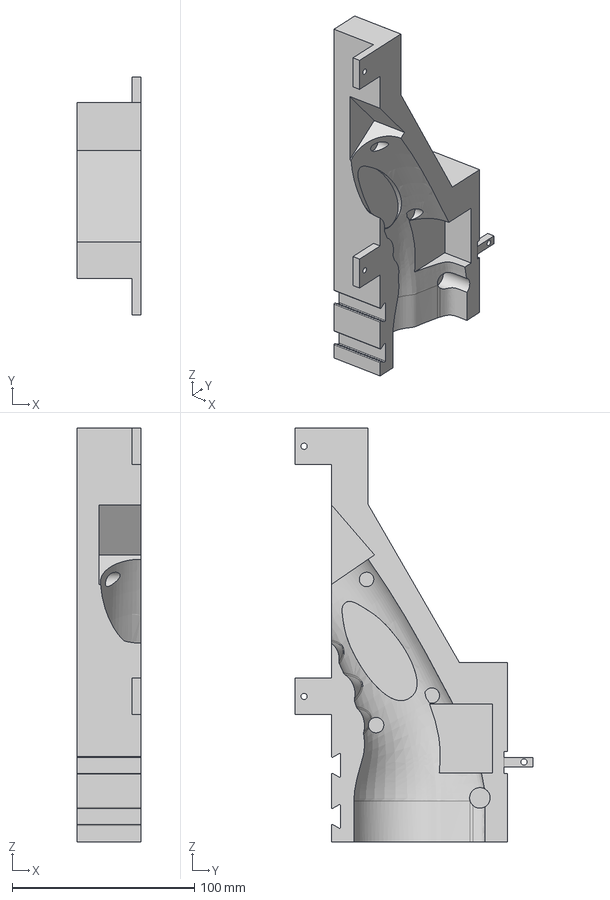
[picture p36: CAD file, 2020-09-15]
CAD/holder-left.step
35.0 x 130.5 x 226.9 mm

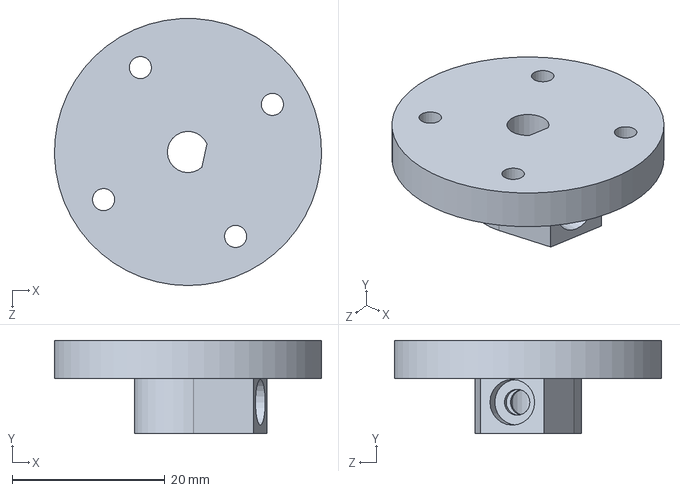
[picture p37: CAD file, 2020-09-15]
CAD/Wheel_MountsV3.SLDPRT
35.0 x 12.2 x 35.0 mm

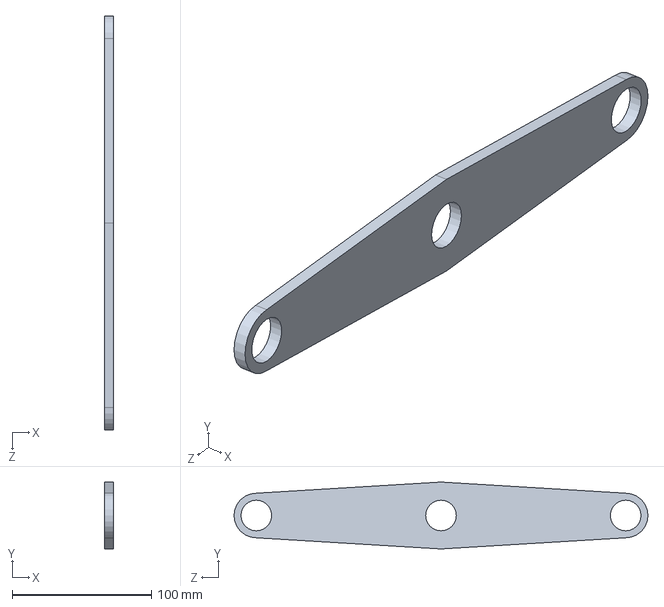
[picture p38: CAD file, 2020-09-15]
CAD/ArmV1.SLDPRT
6.35 x 48.0 x 297.0 mm

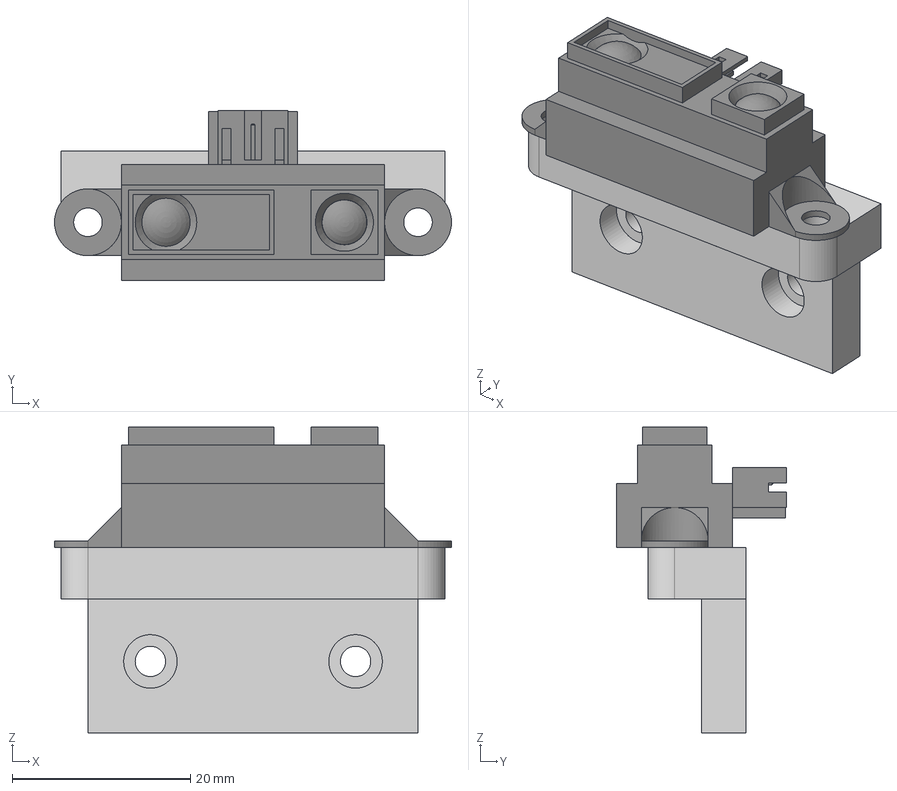
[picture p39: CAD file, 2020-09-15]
CAD/IR_Mount.step
44.5 x 19.0 x 34.2 mm

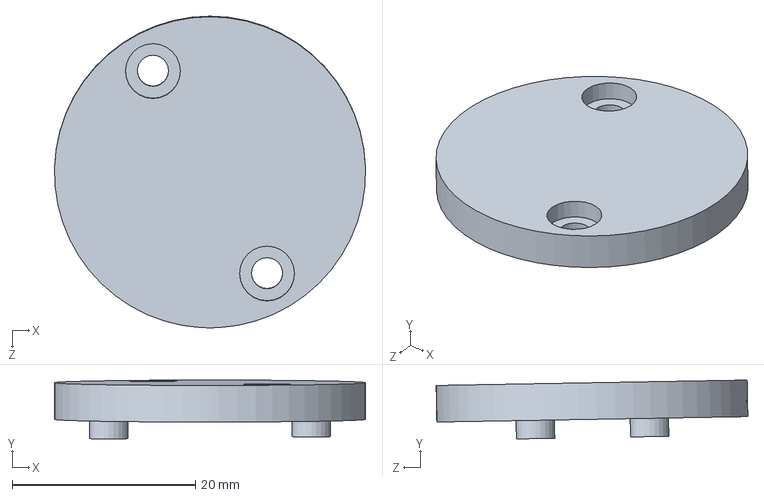
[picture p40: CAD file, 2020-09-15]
CAD/Wheel_Hubcap.sldprt
34.0 x 6.44 x 34.1 mm

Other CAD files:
CAD/608ZZ Mount.sldprt
CAD/LM8UU Bottom Bracket.sldprt
CAD/Ply-Top.SLDPRT
CAD/Ply-Scissor-Top Front.sldprt
CAD/Lead Nut Bolt.sldprt
CAD/Lead Screw Bearing Mount.sldprt
CAD/Lead Screw Nut Mount.sldprt
CAD/MDF_Base.SLDPRT
CAD/Middle Bearing Backing.sldprt
CAD/Middle Bearing Front.sldprt
CAD/Ply-Scissor-Bottom Rear.sldprt
CAD/Ply-Scissor-Top Rear.sldprt
CAD/Top Front Rod Mount.sldprt
CAD/Top Rear Rod Mount.sldprt

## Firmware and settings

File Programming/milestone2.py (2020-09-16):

class VideoStream:
	def __init__(self, src=0, resolution=(320, 240),
		framerate=32):
		# check to see if the picamera module should be used
		# only import the picamera packages unless we are
		# explicity told to do so -- this helps remove the
		# requirement of `picamera[array]` from desktops or
		# laptops that still want to use the `imutils` package
		from cv_lib import PiVideoStream
		# initialize the picamera stream and allow the camera
		# sensor to warmup
		self.stream = PiVideoStream(resolution=resolution,
				framerate=framerate)
    def start(self):
		# start the threaded video stream
		return self.stream.start()
	def update(self):
		# grab the next frame from the stream
		self.stream.update()
	def read(self):
		# return the current frame
		return self.stream.read()
	def stop(self):
		# stop the thread and release any resources
		self.stream.stop()

import imutils
import time
import cv2
import numpy as np
import RPi.GPIO as GPIO
import Adafruit_GPIO.SPI as SPI
import Adafruit_MCP3008
DIR1 = 29  # Direction GPIO PIN
STEP1 = 31 # Step GPIO Pin
DIR2 = 33
STEP2 = 35 # Step GPIO Pin
DIR3 = 36
STEP3 = 38 # Step GPIO Pin
DIR4 = 37
STEP4 = 40   # Step GPIO Pin
#ZSTEP =
#ZDIR =
CW = 1    # Clockwise Direction
CCW = 0   # CCW rotation
wheel_delay = 0.003
z_delay = 0.001
GPIO.setmode(GPIO.BOARD)
GPIO.setup(DIR1,GPIO.OUT)
GPIO.setup(STEP1,GPIO.OUT)
GPIO.setup(DIR2,GPIO.OUT)
GPIO.setup(STEP2,GPIO.OUT)
GPIO.setup(DIR3,GPIO.OUT)
GPIO.setup(STEP3,GPIO.OUT)
GPIO.setup(DIR4,GPIO.OUT)
GPIO.setup(STEP4,GPIO.OUT)
# initialize the video stream and allow the cammera sensor to warmup
vs = VideoStream().start()
time.sleep(2.0)
mcp = Adafruit_MCP3008.MCP3008(clk=CLK, cs=CS, miso=MISO, mosi=MOSI)
# loop over the frames from the video stream
def move_insert(dist_to_steps):
	v = (mcp.read_adc(0) / 1023.0) * 3.3
	dist = 43.543*((v+0.30221)**(-1.5281))
	in_steps = dist*dist_to_steps
    GPIO.output(DIR2,CW)
    GPIO.output(DIR4,CCW)
	for go in range(in_steps):
		GPIO.output(STEP2, GPIO.HIGH)
		GPIO.output(STEP4, GPIO.LOW)
		sleep(wheel_delay)
		GPIO.output(STEP2,GPIO.LOW)
		GPIO.output(STEP4,GPIO.HIGH)
		sleep(wheel_delay)

	if (GPIO.input(7)):
		return True
	else:
		GPIO.output(DIR2,CCW)
	    GPIO.output(DIR4,CW)
		for go in range(in_steps):
			GPIO.output(STEP2, GPIO.HIGH)
			GPIO.output(STEP4, GPIO.LOW)
			sleep(wheel_delay)
			GPIO.output(STEP2,GPIO.LOW)
			GPIO.output(STEP4,GPIO.HIGH)
			sleep(wheel_delay)
		return False
    '''
    IR Sensor reading distance -> Steps -> move motor for x steps

    then if limit switch is pressed, we good
    if not, reset and exit function
    '''
    return 0

def move_align(lateral,vertical,conversion,step_dist_convert):
    if lateral < 0:
        '''
        TENTATIVE: Adjust CW and CCW if needed
        '''
        GPIO.output(DIR1,CW)
        GPIO.output(DIR3,CCW)
    elif lateral > 0:
        GPIO.output(DIR1,CCW)
        GPIO.output(DIR3,CW)

    if vertical > 0:
        GPIO.output(ZDIR,CW)
    elif vertical < 0:
        GPIO.output(ZDIR,CCW)

    if lateral != 0:
        dist = conversion*abs(lateral)
        steps = step_dist_convert*dist
        for i in range(steps):
            GPIO.output(STEP1, GPIO.HIGH)
            GPIO.output(STEP3, GPIO.LOW)
            sleep(wheel_delay)
            GPIO.output(STEP1,GPIO.LOW)
            GPIO.output(STEP3,GPIO.HIGH)
            sleep(wheel_delay)
	return True
    '''
    UNDER CONSTRUCTION FOR VERTICAL
    NEED MORE TRIG AND MATH
    if vertical != 0:
    '''
def vision():
	frame = vs.read()
	frame = imutils.resize(frame, width=400)
    image = cv2.cvtColor(frame, cv2.COLOR_BGR2HSV)
    lower = np.array([170,25,0])
    upper = np.array([255,255,255])
    mask = cv2.inRange(image, lower, upper)
    height, width, depth = frame.shape
    mx = int(width/2)
    my = int(height/2)
    contours,h = cv2.findContours(mask,cv2.RETR_EXTERNAL, cv2.CHAIN_APPROX_NONE)
    if len(contours) != 0:
        # Draw only the contour with the largest area
        for contour in contours:
            (x,y,w,h) = cv2.boundingRect(contour)
            #if w*h>200000 and w*h<5000000:
            if w/h < 5.6 and w/h>5.4 and w*h>780 and w*h<800:
                cv2.rectangle(frame, (x,y), (x+w,y+h), (0,255,0), 1)
                cv2.line(frame,(x+int(w/2),y-length),(x+int(w/2),y+h+length),(0, 0, 255), 1)
				print("Area:{} pixels".format(w*h))
                print('Conversion: 11/{}={} cm/pix'.format(w,11/w))
				return True,x+int(w/2)-mx,my-y+int(h/2),11/w,frame


GPIO.output(DIR1,CW) #Change Direction if needed
GPIO.output(DIR3,CCW)
stop = False
max_setup_width_in_steps = 00000
step_dist_convert = 0000000
while True:
	# grab the frame from the threaded video stream and resize it
	# to have a maximum width of 400 pixels
	for k in range(max_setup_width_in_steps):
		stop, x_dist,y_dist,convert,Frame = vision()
		if stop:
			break
		GPIO.output(STEP1, GPIO.HIGH)
		GPIO.output(STEP3, GPIO.LOW)
		sleep(wheel_delay)
		GPIO.output(STEP1,GPIO.LOW)
		GPIO.output(STEP3,GPIO.HIGH)
		sleep(wheel_delay)

    if x_dist > threshold and y_dist > zthreshold:    #if bot is not aligned
        move_align(x_dist,0,convert) #lateral distance, vertical distance, conversion factor
    else:
        insert_complete = move_insert()
	if insert_complete:
		break

	# show the frame
	cv2.imshow("Frame", Frame)
	key = cv2.waitKey(1) & 0xFF
	# if the `q` key was pressed, break from the loop
	if key == ord("q"):
		break
# do a bit of cleanup
cv2.destroyAllWindows()
vs.stop()

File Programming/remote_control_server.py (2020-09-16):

import socket
import keyboard
from time import sleep
s = socket.socket(socket.AF_INET, socket.SOCK_STREAM)
Port = 8080
maxConn = 999
IP = 'LAPTOP-4CCTQVLJ'

s.bind((IP,Port))
s.listen(0)
print("Server started at"+IP+" on port "+str(Port))

(client_socket,adr) = s.accept()

print('New connection made!')
while True:
    if keyboard.is_pressed('w'):
        client_socket.send(bytes("W","utf-8"))
        print('sent W')
        sleep(0.05)
    elif keyboard.is_pressed('a'):
        client_socket.send(bytes("A","utf-8"))
        print('sent A')
        sleep(0.05)
    elif keyboard.is_pressed('d'):
        client_socket.send(bytes("D","utf-8"))
        print('sent D')
        sleep(0.05)
    elif keyboard.is_pressed('s'):
        client_socket.send(bytes("S","utf-8"))
        print('sent S')
        sleep(0.05)
    elif keyboard.is_pressed('q'):
        client_socket.send(bytes("Q","utf-8"))
        print('sent Q')
        sleep(0.05)
    elif keyboard.is_pressed('e'):
        client_socket.send(bytes("E","utf-8"))
        print('sent E')
        sleep(0.05)
    elif keyboard.is_pressed('z'):
        client_socket.send(bytes("Z","utf-8"))
        sleep(0.05)
        print('sent Z')
    elif keyboard.is_pressed('m'):
        client_socket.send(bytes("M","utf-8"))
        print('sent M')
        print('breaking')
        break
